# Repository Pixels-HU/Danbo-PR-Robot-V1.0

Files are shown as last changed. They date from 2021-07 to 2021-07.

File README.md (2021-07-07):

# Danbo-PR-Robot-V1.0
hDanbo1

# Description
Danbo pr robot is a robot that distributes flyers among people. It makes a speech about pixels. We first use 2 arduino uno for the transmitting and receiving parts, we connect between them using nrf. We use driver circuits for motors and amplifier circuit for speaker.

Danbo1

# Components used
1- Arduino Uno 
https://ram-e-shop.com/product/kit-arduino-uno/

2- Dc Motors
https://store.fut-electronics.com/products/dc-motor-with-metal-gear-3-2-kg-cm-133-rpm-6v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

3- Servo Motor (15 kg.cm)
https://ram-e-shop.com/product/servo-motor-with-magnetic-encoder-360-15-5-kg-cm-metal-gears-fb5311m/

4-Servo 10kg.cm
https://ram-e-shop.com/product/servo-mg995/

5- lm386
https://free-electronic.com/product/lm741cn/

6- Ceramic capacitor 100n f
https://free-electronic.com/product/ceramic-capacitor-100nf-50v/

7- Electrolytic capacitor 1000u
https://free-electronic.com/product/irf540n/

8- Electrolytic capacitor 100uf
https://free-electronic.com/product/electrolytic-capacitor-100uf-50v/

9- IRF540N
https://free-electronic.com/product/irf540n/

10- NRF 24L01
https://free-electronic.com/product/nrf24l01-wireless-module-2-4-ghz-rf-transceiver/

11 - Variable resistance(10k)
https://free-electronic.com/product/potentiometer-wth118-10-kohm/

12- Resistance 470 ohm
https://free-electronic.com/product/resistor-470-ohm-3w/

13- Resistance 10k ohm
https://free-electronic.com/product/resistor-10-kohm-3w/

14- Diode ln4007

15- Resistance 5k

## Mechanical structure
1- 6mm wood (For body)

2- 3mm wood (For head)

3- 6mm acrylic (For gears)

4- M4 Screws (4m) 

5- M4 nuts 

6- 15 Cm Wheels

# Steps to build the mechanical structure

1- Create 3D Model
58710cf5-95d3-4f55-bb44-d71eec74a273fb0c4b6c-20fe-4ef7-932a-8400b34acadbScreenshot (331)Screenshot (332)Screenshot (333)2bd5ae67-7fae-40e5-9a05-6af3d5f4042c9b517ff1-30e2-4df8-80e0-305ad7b346fc49eeb6c1-c135-4f6c-8a2b-e80cf61adb4f

We create a 3D model about Danbo's skeleton using “Solidworks" It would be easier for us to confirm every servo's position and angle of movement in the 3D model. After creating the 3D model, we convert it to 2D for laser cutting. We used 6mm(thickness) wood to laser cut the Danbo body and 3mm (thickness) wood to the Danbo head.

(Hint: You can find the design in the epo, if you are using older version of solidWorks please download the IGS files and drag it and drop it in your solidworks app)

(Hint: you can print the body using the Dxf files in the repo) 

The DXfile in google drive:
https://drive.google.com/drive/folders/12dDjX8gE220Q_c95igGJB5SD7zqggt2-?usp=sharing

2- Servo installation:
WhatsApp Image 2020-12-24 at 10 36 02 AM (3)
WhatsApp Image 2020-12-24 at 10 27 34 AM (1)
There are 2 servos on Danbo's neck, 2 servos for the shoulders

3- Flyers Mechanism :
Assemble the flyer mechanism as shoen in the design

4- Gearbox design:


https://user-images.githubusercontent.com/80456446/124107049-1f808300-da65-11eb-9a47-21ff029a761d.mp4

IMG_0935_(1)
By Gear generator and some calculations, we Design gear box to give us desired velocity and torque. By Gear generator and some calculations, we Design gear box to give us desired velocity and torque.

5- Assemble the body and the head:
WhatsApp Image 2020-12-24 at 10 36 02 AM (1)
WhatsApp Image 2020-12-24 at 10 36 02 AM (3)
WhatsApp Image 2020-12-24 at 10 36 02 AM (4)
WhatsApp Image 2020-12-24 at 10 36 02 AM



https://user-images.githubusercontent.com/80456446/124108085-2b207980-da66-11eb-9232-283778431745.mp4

1- Fix the head plates with screws and nuts

2- Fix the legs together with the body and base

3- Put the wheels and gearbox together in the base plate

4- Fix the arm servos with the arm structure and head servo with the head structure.

## Control
1- Transmitter Stage controller
In this stage we will design the controller of the robot we begin with the circuit design

Components used in this circuit:
In this circuit we use: 
-Arduino UNO

-nrf24l01 module

-two joysticks 

- push bottoms

Schematic:
Danbo2

PCB layout:
Danbo3

Transmitter code of the Arduino:
Uplad the code to your microcontroller, you can find the code in the repo

Shape of the shield:
Danbo4

Driver circuit:
Danbo5

Driver PCB Design:
Danbo6

2- Receiver stage:
In this stage we will get from the controller the buffers and begin to control the robot by several of instructions

Components used in this circuit:
In this stage we use:
-Arduino uno 

-nrf 24l01 module

-our driver circuits. 

- 3 dc motor. 

- 2 servo motor

Receiver code:
Uplad the code to your microcontroller, you can find the code in the repo

3- Speakers
Amplifier circuit:
Danbo7

Amplifier PCB
Danbo8
We use this circuit in order to amplify the sound coming from the speaker.

Speaker's code:
Uplad the code to your microcontroller, you can find the code in the repo

## Pixels'21 Projects video
Our Beautiful Projects 🖤✨
https://www.youtube.com/watch?v=BeQG_2XT7rU&list=PLy8wlMYqB2WyBJAQLZQQEhgkKTbwseKvb

## More Projects
for more projects in different enginneering fields, please visit our wevbsite:
https://pixelseg.com/project-contest
Screenshot (149)

## Pixels App 
187960930_3955292401216930_6844533153445761662_n

“Pixels Egypt” mobile app is considered an important and easy way to stay in touch with us.

The app will help you to:

- Browse different online courses and resources in different fields like Computer, Communication, Power, and Mechanical Engineering.
- You will find courses, videos, books and more.
- Follow our news.
- Share our knowledge.
- Be one of the family.

Get it now on Google Play:

https://play.google.com/store/apps/details

## Follow Pixels:

- Facebook:

https://www.facebook.com/PixelsEgyptOrg

- YouTube:

https://www.youtube.com/c/PixelsEgypt

- Instagram:

https://www.instagram.com/pixelsegypt/

- Twitter:

https://twitter.com/pixelsegypt?lang=en

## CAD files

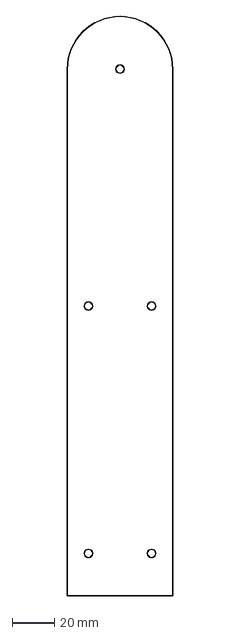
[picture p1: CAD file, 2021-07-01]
mechanical_design/dxf/arm/arm3.DXF
50.0 x 275.0 mm

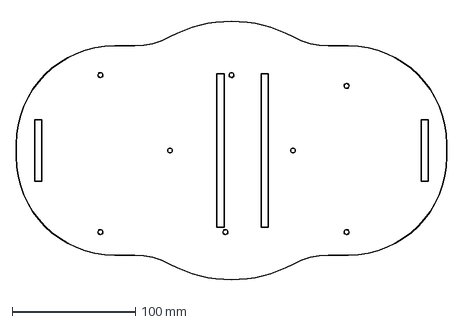
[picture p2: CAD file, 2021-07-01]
mechanical_design/dxf/base/base1.DXF
350.0 x 218.5 mm

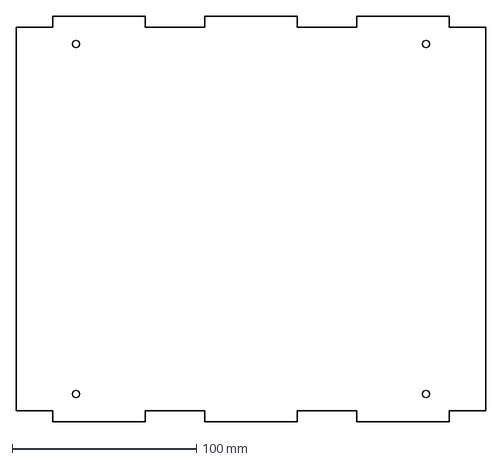
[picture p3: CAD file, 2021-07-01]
mechanical_design/dxf/body/box.DXF
255.0 x 220.0 mm

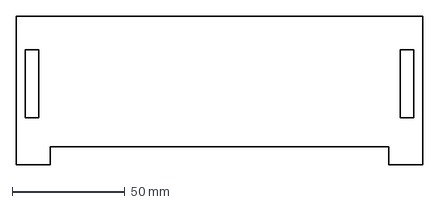
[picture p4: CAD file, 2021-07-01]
mechanical_design/dxf/flyer mechanism/flyer base1.DXF
180.0 x 66.0 mm

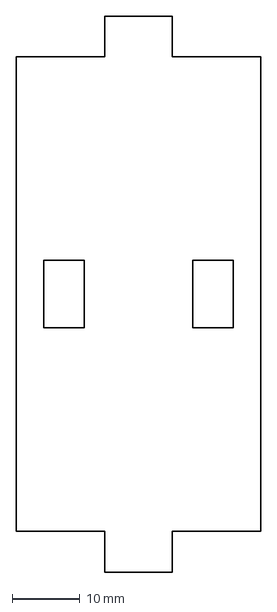
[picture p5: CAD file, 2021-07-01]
mechanical_design/dxf/gearbox/2nd side of gear train.DXF
36.0 x 82.0 mm

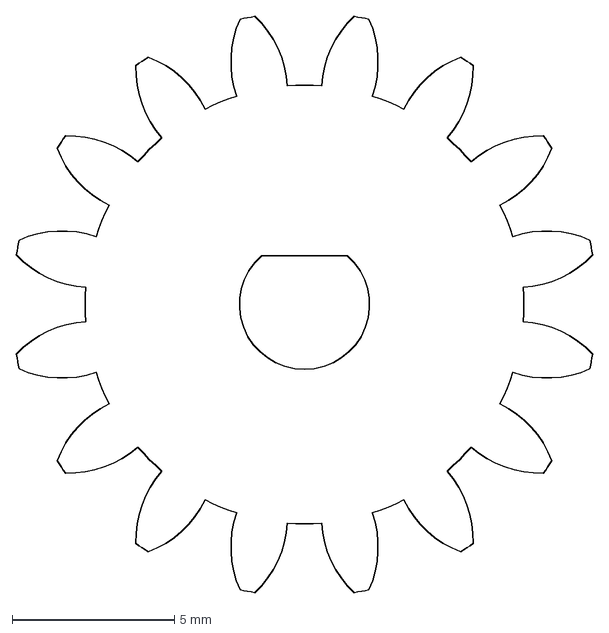
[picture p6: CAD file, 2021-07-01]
mechanical_design/dxf/gearbox/laser cut/input gear .DXF
17.7 x 17.7 mm

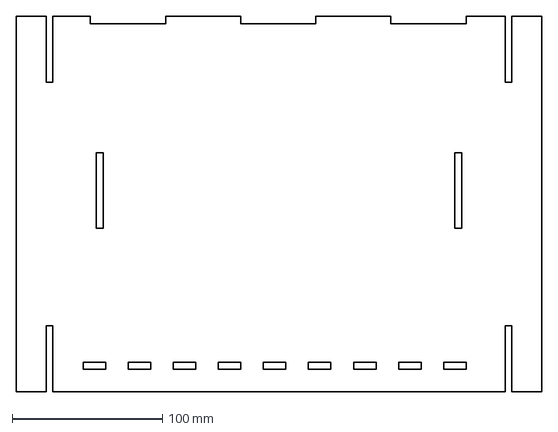
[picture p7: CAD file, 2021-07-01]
mechanical_design/dxf/head dxf/back.DXF
350.0 x 250.0 mm

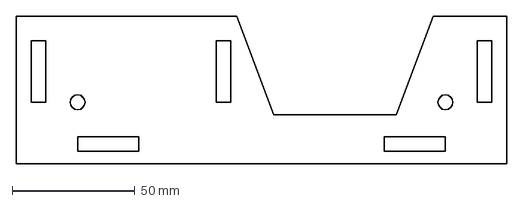
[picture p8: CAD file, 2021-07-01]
mechanical_design/dxf/head/Part20 servo.DXF
200.0 x 60.0 mm

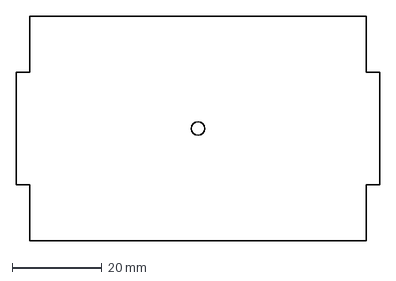
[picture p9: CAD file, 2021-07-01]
mechanical_design/dxf/arm/arm1.DXF
81.0 x 50.0 mm

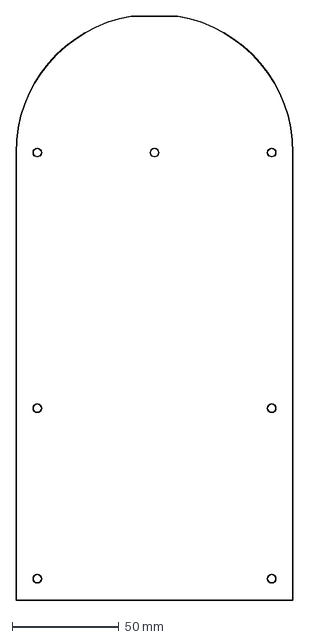
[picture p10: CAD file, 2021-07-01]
mechanical_design/dxf/base/leg1.DXF
130.0 x 274.1 mm

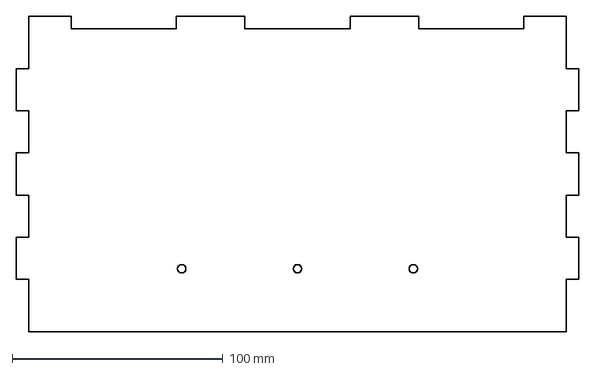
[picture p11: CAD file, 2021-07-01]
mechanical_design/dxf/body/leg body.DXF
267.0 x 150.0 mm

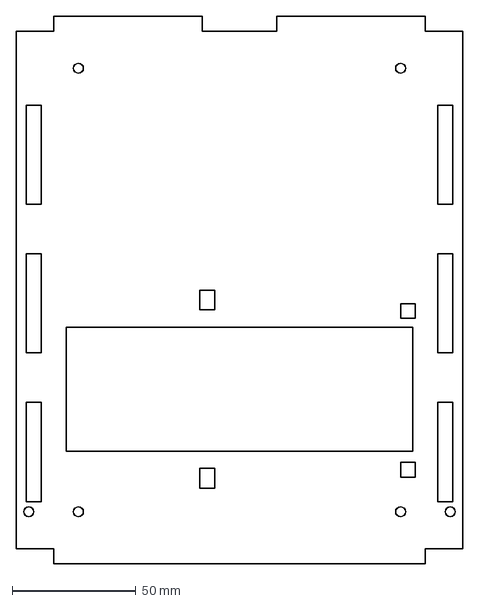
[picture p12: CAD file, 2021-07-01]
mechanical_design/dxf/flyer mechanism/flyer base2.DXF
180.0 x 221.0 mm

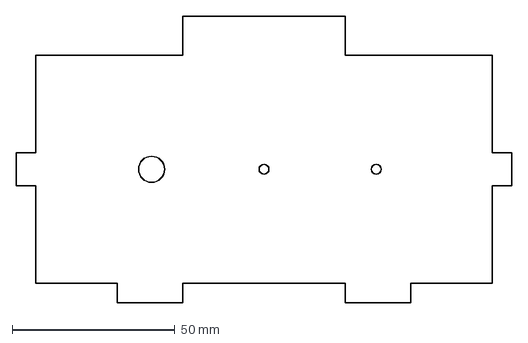
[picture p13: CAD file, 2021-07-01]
mechanical_design/dxf/gearbox/laser cut/side of gear train 2.DXF
152.0 x 88.0 mm

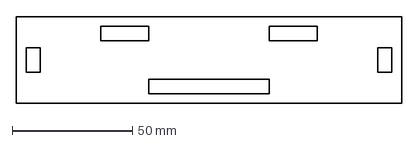
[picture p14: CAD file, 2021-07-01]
mechanical_design/dxf/gearbox/top of gear train.DXF
160.0 x 36.0 mm

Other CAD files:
mechanical_design/dxf/head dxf/side 1 (4).DXF
mechanical_design/dxf/head/Part4 servo.DXF
mechanical_design/dxf/arm/arm2.DXF
mechanical_design/dxf/base/leg2.DXF
mechanical_design/dxf/body/arm base2.DXF
mechanical_design/dxf/body/body base.DXF
mechanical_design/dxf/body/body1.DXF
mechanical_design/dxf/body/body2.DXF
mechanical_design/dxf/body/door.DXF
mechanical_design/dxf/body/head base.DXF
mechanical_design/dxf/flyer mechanism/flyer base 3.DXF
mechanical_design/dxf/gearbox/laser cut/2nd side of gear train(2times).DXF
mechanical_design/dxf/gearbox/laser cut/base of gear train.DXF
mechanical_design/dxf/gearbox/laser cut/mid large gear.DXF
mechanical_design/dxf/gearbox/laser cut/mid small gear.DXF
mechanical_design/dxf/gearbox/laser cut/output gear L.DXF
mechanical_design/dxf/gearbox/laser cut/output gear R.DXF
mechanical_design/dxf/gearbox/laser cut/output gear.DXF
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

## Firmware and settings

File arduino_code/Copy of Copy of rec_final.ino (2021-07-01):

#include <RHReliableDatagram.h>
#include <RH_NRF24.h>
 void servoPulse (int servo, int angle); //function of operation
// Include dependant SPI Library 
#include <SPI.h>
 
// Define addresses for radio channels
#define CLIENT_ADDRESS 1   
#define SERVER_ADDRESS 2
 
// Motor A Connections
//int enA = 10;
//int in1 = 10;
//int in2 = 4;
int in1=9;
//aduio player/
//TMRpcm tmrpcm;

// Motor B Connections
//int enB = 9;
//int in3 = 7;
//int in4 = 6;
int in2 =3;

//motor c
int in3=4;

//servo motors
int servo1 = 6;
int servo2 = 5;
int angle;
int pwm;
// Create an instance of the radio driver
RH_NRF24 RadioDriver;
 
// Sets the radio driver to NRF24 and the server address to 2
RHReliableDatagram RadioManager(RadioDriver, SERVER_ADDRESS);
 
// Define a message to return if values received
uint8_t ReturnMessage[] = "JoyStick Data Received"; 

// Define the Message Buffer
uint8_t buf[5];
  
void setup()
{
  // Setup Serial Monitor
  Serial.begin(9600);
  
  // Set all the motor control pins to outputs
//  pinMode(enA, OUTPUT);
  //pinMode(enB, OUTPUT);
  pinMode(in1, OUTPUT);
  pinMode (servo1,OUTPUT);
  pinMode (servo2, OUTPUT);
  pinMode(in2, OUTPUT);
  pinMode(in3, OUTPUT);
  //pinMode(in4, OUTPUT);
  pinMode(2,OUTPUT);
  digitalWrite(2,LOW);
  // Initialize RadioManager with defaults - 2.402 GHz (channel 2), 2Mbps, 0dBm
  if (!RadioManager.init())
    Serial.println("init failed");
} 
 
void loop()
{
  if (RadioManager.available())
  {
 // Wait for a message addressed to us from the client
    uint8_t len = sizeof(buf);
    uint8_t from;
    if (RadioManager.recvfromAck(buf, &len, &from))
 
    {
 
      //Serial Print the values of joystick
      Serial.print("got request from : 0x");
      Serial.print(from, HEX);
      Serial.print(": MotorA = ");
      Serial.print(buf[0]);
      Serial.print(" MotorB = ");
      Serial.print(buf[1]);
      Serial.print(" servo = ");
      Serial.println(buf[2]);
      Serial.println(buf[3]);
      Serial.println(buf[4]);
      // Set Motor Direction
     /* if (buf[2] == 1)
      {
    // Motors are backwards
    digitalWrite(in1, LOW);
    digitalWrite(in2, HIGH);
    //digitalWrite(in3, LOW);
    //digitalWrite(in4, HIGH);
    }else{
    // Motors are forwards
    digitalWrite(in1, HIGH);
    digitalWrite(in2, LOW);
   // digitalWrite(in3, HIGH);
    //digitalWrite(in4, LOW);
     }
 */
      
      // Drive Motors
      analogWrite(in1, buf[1]);
      analogWrite(in2, buf[0]);
     servoPulse (servo1, (int) buf[2]);
     //delay (50);
      servoPulse (servo2, (int) buf[2]);
      if(buf[4]==1)
      {
      digitalWrite(in3,HIGH);
      Serial.println("motor on");
      }
      else
      {
        digitalWrite(in3,LOW);
      }
      // Send a reply back to the originator client, check for error
      if (!RadioManager.sendtoWait(ReturnMessage, sizeof(ReturnMessage),&from))
        Serial.println("sendtoWait failed");
    }
  }              
}

//servo function
void servoPulse (int servo, int angle)
{
 pwm = (angle*11) + 500;      // Convert angle to microseconds
 digitalWrite(servo, HIGH);
 delayMicroseconds(pwm);
 digitalWrite(servo, LOW);
//delay(50);                   // Refresh cycle of servo
}

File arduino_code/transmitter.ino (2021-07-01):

#include <RHReliableDatagram.h>
#include <RH_NRF24.h> 
#include <SPI.h>
#define joyVert A1 
#define joyHorz A0
#define joysVert A2
#define joysHorz A3
#define button 7
#define pb 4

// Define Joystick Values - Start at 512 (middle position)
int joyposVert = 512;
int joyposHorz = 512;
int joysposVert = 512;
int joysposHorz = 512;
boolean state=0;
#define CLIENT_ADDRESS 1   
#define SERVER_ADDRESS 2

// Create an instance of the radio driver
RH_NRF24 RadioDriver;

// Sets the radio driver to NRF24 and the client address to 1
RHReliableDatagram RadioManager(RadioDriver, CLIENT_ADDRESS);

// Declare unsigned 8-bit motorcontrol array
// 2 Bytes for motor speeds plus 1 byte for direction control
uint8_t motorcontrol[7]; 
//uint8_t motorcontrol[5]; 

// Define the Message Buffer
uint8_t buf[5];

void setup()
{
  // Setup Serial Monitor
  Serial.begin(9600);
 
  // Initialize RadioManager with defaults - 2.402 GHz (channel 2), 2Mbps, 0dBm
  if (!RadioManager.init())
    Serial.println("init failed");
  pinMode(button,INPUT_PULLUP);
  pinMode(pb,INPUT_PULLUP);
  pinMode(joysVert,INPUT);
  pinMode(joysHorz,INPUT);

  // Set initial motor direction as forward
  motorcontrol[2] = 90;
 motorcontrol[3]=0;
}

void loop()
{
  // Print to Serial Monitor
  Serial.println("Reading motorcontrol values ");
  
  // Read the Joystick X and Y positions
  joyposVert = analogRead(joyVert); 
  joyposHorz = analogRead(joyHorz);
  joysposVert = analogRead(joysVert); 
  joysposHorz = analogRead(joysHorz);
//heaad part
  if (joysposVert <460)
  {
    motorcontrol[2]=map(joysposVert,460,0,90,0); 
  }
  else if (joysposVert >560)
  {   
    motorcontrol[2]=map(joysposVert,560,1023,90,180); 
    }
else
  {
    // This is Stopped
    motorcontrol[2] = 90;
} 
    if (joysposHorz <460)
  {
    motorcontrol[2]=map(joysposHorz,0,460,0,90); 
  }
  else if (joysposHorz >560)
  {   
    motorcontrol[2]=map(joysposHorz,560,1023,90,180); 
    }
else
  {
    // This is Stopped
    motorcontrol[5] = 90;
}//base part

  if (joyposVert < 460)
  { 
    //set direction backwards
  //  motorcontrol[2]=1; 
    motorcontrol[0] = map(joyposVert, 460, 0, 0, 255);
    motorcontrol[1] = map(joyposVert, 460, 0, 0, 255);

  }
  else if (joyposVert > 564)
  {
    // This is Forward
    // Set Motors forward
    //motorcontrol[2] = 0;

    //Determine Motor Speeds
    motorcontrol[0] = map(joyposVert, 564, 1023, 0, 255);
    motorcontrol[1] = map(joyposVert, 564, 1023, 0, 255); 

  }
  else
  {
    // This is Stopped
    motorcontrol[0] = 0;
    motorcontrol[1] = 0;
//    motorcontrol[2] = 0; 

  }
  
  // Now do the steering
  // The Horizontal position will "weigh" the motor speed
  // Values for each motor

  if (joyposHorz < 460)
  {
    // Move Left
    // As we are going left we need to reverse readings
    // Map the number to a value of 255 maximum
    joyposHorz = map(joyposHorz, 460, 0, 0, 255);

    motorcontrol[0] = motorcontrol[0] - joyposHorz;
    motorcontrol[1] = motorcontrol[1] + joyposHorz;

    // Don't exceed range of 0-255 for motor speeds
    if (motorcontrol[0] < 0)motorcontrol[0] = 0;
    if (motorcontrol[1] > 255)motorcontrol[1] = 255;

  }
  else if (joyposHorz > 564)
  {
    // Move Right
    // Map the number to a value of 255 maximum
    joyposHorz = map(joyposHorz, 564, 1023, 0, 255);
  
    motorcontrol[0] = motorcontrol[0] + joyposHorz;
    motorcontrol[1] = motorcontrol[1] - joyposHorz;

    // Don't exceed range of 0-255 for motor speeds
    if (motorcontrol[0] > 255)motorcontrol[0] = 255;
    if (motorcontrol[1] < 0)motorcontrol[1] = 0;      

  }

  // Adjust to prevent "buzzing" at very low speed
  if (motorcontrol[0] < 8)motorcontrol[0] = 0;
  if (motorcontrol[1] < 8)motorcontrol[1] = 0;
  state = digitalRead(pb);
  if(state==LOW)
  {
    //motorcontrol[0]=0;
  motorcontrol[4]=1;
 //   delay(200);
  }
  else
  {
    motorcontrol[4]=0; 
  }
//  motorcontrol[6]=0;
/*  if(pb==0)
  {
  //motorcontrol[4]=1;
  }
else
  motorcontrol[4]=0;
*/
  //Display the Motor Control values in the serial monitor.
  Serial.print("Motor A: ");
  Serial.print(motorcontrol[0]);
  Serial.print(" - Motor B: ");
  Serial.print(motorcontrol[1]);
  Serial.print(" - Direction: ");
  Serial.println(motorcontrol[2]);
  Serial.println(motorcontrol[3]);
  Serial.println(motorcontrol[4]);

  //Send a message containing Motor Control data to manager_server
  if (RadioManager
  .sendtoWait(motorcontrol, sizeof(motorcontrol), SERVER_ADDRESS))
  {
    Serial.print(" start sending ");
    // Now wait for a reply from the server
    uint8_t len = sizeof(buf);
    uint8_t from;
    if (RadioManager.recvfromAckTimeout(buf, &len, 2000, &from))
    {
      Serial.print("got reply from : 0x");
      Serial.print(from, HEX);
      Serial.print(": ");
      Serial.println((char*)buf);
    }
    else
    {
      Serial.println("No reply, is nrf24_reliable_datagram_server running?");
    }
  }
  else
    Serial.println("sendtoWait failed");

//delay(10); // Wait a bit before next transmission
}
